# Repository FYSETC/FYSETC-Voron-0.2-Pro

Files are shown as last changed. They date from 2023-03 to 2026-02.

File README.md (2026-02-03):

# FYSETC-Voron-0.2-Pro

This is a project from the VORON community, VORON 0.2. We made a little upgrade and improvement on the basis of this project, and provided a complete set of information. Thanks to the open source materials and support provided by the VORON community, and hope you like it. You can find Voron official information below.

1.VORON 0.2 Official website：https://vorondesign.com/voron0.2

2.VORON 0.2 Official Github：https://github.com/VoronDesign/Voron-0

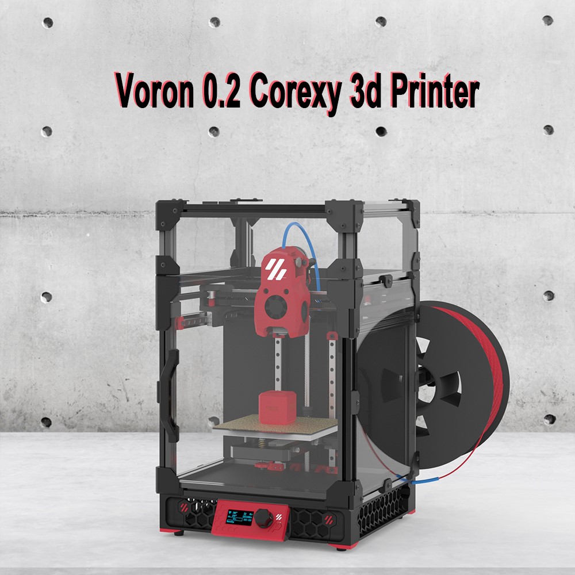
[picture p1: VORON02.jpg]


## 1. Kit advantages:

1.VORON 0 1.3-inch OLED display

2.One-piece CNC hotbed holder 

3.Tophat cover (you can lift the top cover at any time for more convenient maintenance)

4.Sensorless Homing 

5.Upgrade MINI Stealthburner head

6.CNC Lightweight Gantry

7.Print surface: high-quality powder PEI steel plate, good adhesion, flexibility, easy to take molds; platform: MIC6 aluminum finishing, flatness up to 0.05, attached to high-temperature soft magnetic, and additionally designed positioning pillars, which can be fast Place the steel plate in place and not easily move.

8.Sailfish High Flow Hotend（24V 60W）

9.Provide a complete set of crimped terminal Teflon wires, suitable in length, plug and play, and easy to use.

10.It adopts high-precision Stainless steel 440c linear guide MGN7H Z1, precise position and stable operation.

11.Imported silicone thermal mattress, high temperature resistance, built-in over-temperature fuse, high power 24V 75W, fast heating.

12.High-quality motors.

13.Sherpa nano-coating one-piece helical gear kit 

14.Use Klipper firmware
Running on CATALYST V2.0 Motherboard +CM68 Linux core board (based on RK3568, 2GB+32GB) +M36 HUB V1.1 , it can achieve higher printing speed, provide Web control (via WiFi or Ethernet), can connect to a camera.

15.VORON 0 LED light 

## 2. Details

[Voron 0.2 Pro](https://github.com/FYSETC/FYSETC-Voron-0.2/blob/main/0.2/README.md)

[Voron 0.2 R1 Pro](https://github.com/FYSETC/FYSETC-Voron-0.2/blob/main/0.2%20R1/README.md)

[Voron 0.2 R1 Pro V1.1](https://github.com/FYSETC/FYSETC-Voron-0.2-Pro/blob/Pro_R1_1.1/0.2%20R1%20V1.1/README.md)

[Voron 0.2 R1 Pro V1.2](https://github.com/FYSETC/FYSETC-Voron-0.2-Pro/blob/Pro_R1_1.1/0.2%20R1%20V1.2/README.md)

## 3. Community

[Voron community](https://discord.gg/voron)

[FYSETC Facebook group](https://www.facebook.com/groups/238970713918171)

## 4. Buy link

[Aliexpress](https://www.aliexpress.com/item/3256805648574097.html)

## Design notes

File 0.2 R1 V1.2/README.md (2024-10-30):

# Introduction

This is a project from the VORON community, VORON 0.2. We made a little upgrade and improvement on the basis of this project, and provided a complete set of information. Thanks to the open source materials and support provided by the VORON community, and hope you like it. You can find Voron official information below.

1. VORON 0.2 R1 Official website：

https://vorondesign.com/voron0.2

2. VORON 0.2 R1 Official Github:

https://github.com/VoronDesign/Voron-0

# Feature

The new **Voron 0. 2 R1 Pro V1.2 Kit** has a new design for the electronic part, which is easier to connect and configure, and is as close as possible to out-of-the-box use.

# BOM

[Voron 0.2 R1 Pro V1.2](https://github.com/FYSETC/FYSETC-Voron-0.2-Pro/blob/Pro_R1_1.1/0.2%20R1%20V1.2/BOM.md)

# STL changes

Check it.STL has not been modified and can continue to be used [here](https://github.com/FYSETC/FYSETC-Voron-0.2-Pro/tree/Pro_R1_1.1/0.2%20R1%20V1.1/STL).

### Hotend Mount

Check it. [here](https://github.com/FYSETC/FYSETC-Voron-0.2-Pro/tree/main/0.2%20R1%20V1.1/STL/Toolheads/Hotend_Mounts/Fan_Saver)

# Wiring

### R1 Pro V1.1 kit

Following is our Catalyst board wiring diagram for VORON 0.2 R1 Pro V1.1 kit.

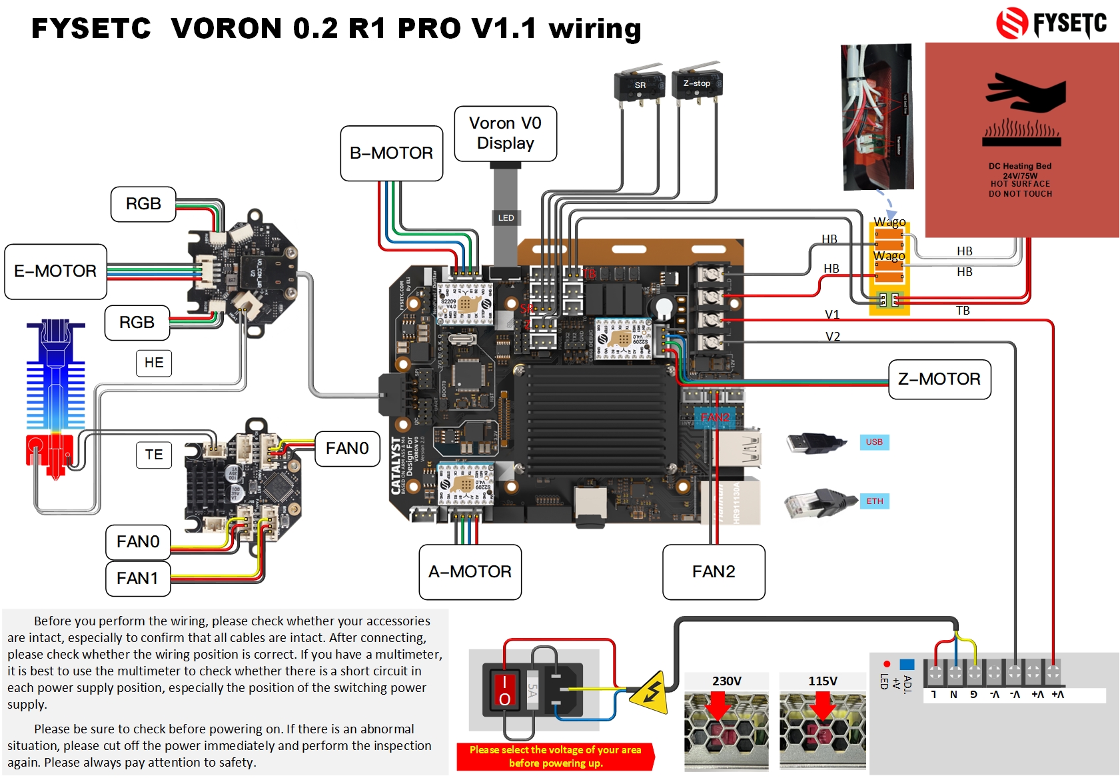
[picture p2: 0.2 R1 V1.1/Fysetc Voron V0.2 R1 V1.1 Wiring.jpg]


# Installation Guide 

Check VORON Assembly manual [here](https://github.com/VoronDesign/Voron-0/tree/Voron0.2/Manuals).

### Page 18 "FRAME - NUT ADAPTER STRIPS"

Kit already comes with PCB style strips to fix the rails

### Page 36 "FRAME - COMPONENT PREP"

Check video [here](https://youtu.be/7Pc5haeAJ8E?si=1WgsYohBYdl78QiE&t=1348)

### Page 120 "X AXIS"

Check video [here](https://youtu.be/7Muv3Jlx758?si=al9ezyuIO8-YeGr-&t=477)

### Page 190 "ELECTRONICS & WIRING"

Following the Catalyst board wiring diagram for VORON 0.2 R1 Pro V1.1 kit.

Check it [here](https://github.com/FYSETC/FYSETC-Voron-0.2-Pro/blob/main/0.2%20R1%20V1.1/Fysetc%20Voron%20V0.2%20R1%20V1.1%20Wiring.pdf).

# Firmware&OS

## CM68 OS 
> [!CAUTION]
> ```diff
> + The control board of this kit has been installed with Klipper OS and MCU Klipper firmware at the factory.
> + And it's pre-configured.
> + As long as the wiring is correct, it can be used after power on.
> - Do not perform the following steps unless you are sure you want to reinstall the firmware.
> ```

The control board uses the CM68 core based on RK3568 as the upper computer of Klipper. Its system is compiled based on Debian 10, and the environment and plug-ins required by Klipper are pre-installed. After burning, it can be used directly.

In general, the pre-installed system can be used directly without re-flashing, unless you encounter unsolvable program problems.

The OS of CM68:

The factory OS is here：
https://github.com/FYSETC/Catalyst_Kit_V2.0/blob/main/software/update_voron0.2_20240108.rar

https://drive.google.com/file/d/1JBLMIpcVtEe9ST9WWUlaOP-ofm4k7y5c/view?usp=drive_link

Update steps:

1. Power on VORON with AC Power. Then plug in the USB3.0 A-A cable into the interface on the upper layer of the blue USB3.0 socket.
2. Open the "RKDevTool_Release",
4. Click the Upgrade Firmware (升级固件) tab, click the Firmware (固件) button to select the firmware, and click the Upgrade button to upgrade  
     
   After selected firmware, it will show like as below  
     
5. Hold the recovery button, click the reset button while holding recovery button (No need to hold reset button), when the RKDevTool found device, release the recovery button.
     
6. Wait for the upgrade to complete. Remember not to cut off the power or unplug the data cable during the process, otherwise the upgrade will fail or even damage the CM68.  
     

## MCU Firmware

<p style="color: red">
<strong>
Do not perform the following steps unless you are sure you want to reinstall the firmware.
</strong>
</p>

If you know the structure of Klipper, then you should understand that the firmware of the MCU is compiled and installed by the host computer (CM68). This is the way we recommend.

Of course, you can also use other methods to burn the MCU, such as through the "STM32CubeProgrammer" on the computer, or with the help of burning tools such as STlink. These need to be studied by yourself, and our control board also provides corresponding interfaces.

The MCU model we use is STM32F446RCT6, with an external 8Mhz crystal oscillator, and uses PA11/PA12 as USB communication. The following is the MCU configuration and burning process:

1. MCU enters DFU mode:

   - Powered off the whole machine
   - Use a jumper cap to connect 3V3 and B0(boot0)
     [img]()
   - Power on the whole machine and wait for it to start

2. Use putty or similar SSH tools to connect to CM68 using IP or host name

    ```
    host name: voron-02-pro.local
    Username: linaro
    Password: linaro
    If you are not very familiar with linux, do not use the root user to log in. Misoperation may cause damage to the system.
    Username: root
    Password: root
    ```

3. Configure the firmware:

    - use "lsusb" to ensure the mcu enter dfu mode,

       ```
       lsusb
       ```

    - configure the firmware
    
       ```
       cd ~/klipper
       make clean
       make menuconfig
       ```
       
4. update the firmware and reboot

    - Compile and burn the firmware:
    
      ```
       make flash FLASH_DEVICE=0483:df11
      ```
    
    - Powered off the whole machine
    - Use a jumper cap to connect B0(boot0) and G(GND)
    - Power on the whole machine and wait for it to start
  
5.If you need update the M36 tool Board,Please refer to https://github.com/FYSETC/M36_HUB_V1

# Print

## Connect via Ethernet

The control board defaults to obtain IP automatically, make sure your router can provide DHCP service normally. You only need to plug in the Internet cable, and when you see the green and yellow lights on, indicates that it is connected to the network.

You have two methods to login the mainsail webpage:

### IP address
you need to go to your router to find the device named voron-02-pro, and write down the IP address
### Host name
The kit has already installed the required plug-ins, and you can access the mainsail page through the pre-set host name: voron-02-pro.local

## Connect via WiFi

- First connect the machine to your LAN via Ethernet, make sure you can log in to CM68 via SSH.
- Plug the included USB wifi into any USB interface on CATALYST board
- Use the following command checks whether the wifi module is recognized:
```
sudo ifconfig
```
- Use the following command to connect to wifi
```
sudo wifi_sta_start.sh ssid password
```
- Use the following command checks whether the wifi module is connected to your router, and get the ip address:
```
sudo ifconfig
```

# FAQ

## 1. Can't find mcu/unable to connect to mcu
Reason:
       It may be that the status of boot0 is uncertain, causing the STM32 to enter the DFU mode, resulting in the connection error.
Solution:
   - Powered off the whole machine
   - Use a jumper cap to connect B0(boot0) and G(GND)
   - Power on the whole machine and wait for it to start
## 2. Mcu firmware version too low
Reason:
The factory version of the Klipper host is the same as that of the MCU. Maybe you have clicked the update button on the mainsail webpage to update the Klipper host. As a result, the version of the host is newer than the firmware of the MCU.
Solution:
update the mcu firmware: Refer to the Firmware&OS==>MCU Firmware
## 3. Temperature error
Reason:
You may have forgotten to connect the MX3.0 16P cable, or it may not be connected firmly.
Solution:
Make sure the MX3.0 16P cable is connected and secure.
## 4. How to use the accelerometer
Refer to Klipper document: 
https://www.klipper3d.org/Resonance_Compensation.html

## 5. Wifi Connection Issues
If you are having problems with your Catalyst wifi, please fix using the following solution. 

SSH into the Catalyst, and run the following command `sudo nano /etc/network/interfaces`

Once you have run the command, add the following lines 

```
auto wlan0
iface wlan0 inet dhcp
wpa-ssid Your Network Name Here
wpa-psk Your Password Goes Here
```
example if your wifi name is fysetcwifi and password was ItRocks:
```
auto wlan0
iface wlan0 inet dhcp
wpa-ssid fysetcwifi
wpa-psk ItRocks
```

# Support
Voron community: 
https://discord.gg/voron
FYSETC Facebook group: 
https://www.facebook.com/groups/238970713918171
FYSETC Discord:
https://discord.gg/T3XcJPgr 
# Buy Link
https://www.aliexpress.com/item/3256805648574097.html

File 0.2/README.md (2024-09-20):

# FYSETC-Voron-0.2-Pro

This is a project from the VORON community, VORON 0.2. We made a little upgrade and improvement on the basis of this project, and provided a complete set of information. Thanks to the open source materials and support provided by the VORON community, and hope you like it. You can find Voron official information below.

1.VORON 0.2 Official website：https://vorondesign.com/voron0.2

2.VORON 0.2 Official Github：https://github.com/VoronDesign/Voron-0



## 1. Kit advantages:

1.VORON 0 1.3-inch OLED display

2.One-piece CNC hotbed holder 

3.Tophat cover (you can lift the top cover at any time for more convenient maintenance)

4.Sensorless Homing 

5.Upgrade MINI Stealthburner head

6.CNC Lightweight Gantry

7.Print surface: high-quality powder PEI steel plate, good adhesion, flexibility, easy to take molds; platform: MIC6 aluminum finishing, flatness up to 0.05, attached to high-temperature soft magnetic, and additionally designed positioning pillars, which can be fast Place the steel plate in place and not easily move.

8.Tornado hotend, check the features [here](https://github.com/FYSETC/FYSETC-Voron-0/blob/main/Tornado_hotend.md). (Please installation guide on our [youtube](https://www.youtube.com/watch?v=a5HArBp4h3s))

9.Provide a complete set of crimped terminal Teflon wires, suitable in length, plug and play, and easy to use.

10.It adopts high-precision Stainless steel 440c linear guide, precise position and stable operation

11.Imported silicone thermal mattress, high temperature resistance, built-in over-temperature fuse, high power 24V 75W, fast heating.

12.High-quality motors.

13.Contains VORON V0 UMBILICAL FRAME and VORON V0 UMBILICAL TOOL HEAD

14.Use Klipper firmware
Running on Cheetah v3.0 and Raspberry Pi 4 2GB, it can achieve higher printing speed, provide Web control (via WiFi or Ethernet), can connect to a camera.

## 2. BOM

[Voron 0.2 Pro](https://github.com/FYSETC/FYSETC-Voron-0.2/blob/main/0.2/BOM.md)

## 3. Modified STLs (2023.03.03)

So we modify these STLs base on the originals. You can find them in our `github` or `gitee`.

`FramePCBCover X1.stl` : For VORON V0 UMBILICAL FRAME[github](https://github.com/FYSETC/FYSETC-Voron-0.2/blob/main/STL/ADD/FramePCBCover%20X1.STL)

`ToolheadSpacer_with_StrainRelief X1`:For VORON V0 UMBILICAL TOOL HEAD [github](https://github.com/FYSETC/FYSETC-Voron-0.2/blob/main/STL/ADD/ToolheadSpacer_with_StrainRelief%20X1.STL)

`VORON0.1 X2.stl` :For CNC Lightweight Gantry [github](https://github.com/FYSETC/FYSETC-Voron-0.2/blob/main/STL/ADD/VORON0.1%20X2.stl)

`LJY-B01 X1.stl`:For One-piece CNC hotbed holder [github](https://github.com/FYSETC/FYSETC-Voron-0.2/blob/main/STL/ADD/LJY-B01%20X1.STL)

`Drag Chain Spacer X1.stl`:For One-piece CNC hotbed holder Chain [github](https://github.com/FYSETC/FYSETC-Voron-0.2/blob/main/STL/ADD/Drag%20Chain%20Spacer%20X1.STL)

## 4. Installation Guide

### 4.1 VORON Assembly manual

Check it [here](https://github.com/VoronDesign/Voron-0/tree/Voron0.2/Manuals).

### 4.2 Tornado Hotend installation

Please check it on our [youtube](https://www.youtube.com/watch?v=a5HArBp4h3s).

## 5. Wiring

Following is our Cheetah v3.0 board wiring diagram for VORON 0.2 pro kit.



## 6. Firmware&OS

After you finish assembling and inspecting, be sure to wire according to the wiring diagram, and make sure that all positive and negative poles are not reversed before powering on. If you have a multimeter, it is best to check again that the power input port is not short-circuited.
Next we start configuring the firmware:
### 6.1. Install the Raspberry Pi

There is a Micro SD Card with the mainsail OS system burned in our kit. The capacity is 16GB. You need to insert it into the card slot of the Raspberry Pi, and connect the Raspberry Pi to the main board with a USB cable and a power cable (it is a 6-core Dupont cable, which contains a serial port, but the power supply is made by default, and the serial port is a spare).

If you need to reinstall the system, you can refer to the following link:
https://docs-os.mainsail.xyz/getting-started/raspberry-pi-os-based

### 6.2. Configure the Cheetah Board

Use SSH software to connect to your Raspberry Pi and enter the following command:
```
lsusb
```
You should see the device as shown below:

If not, please go back and check the power supply and wiring of the motherboard to ensure that each power indicator light is on.
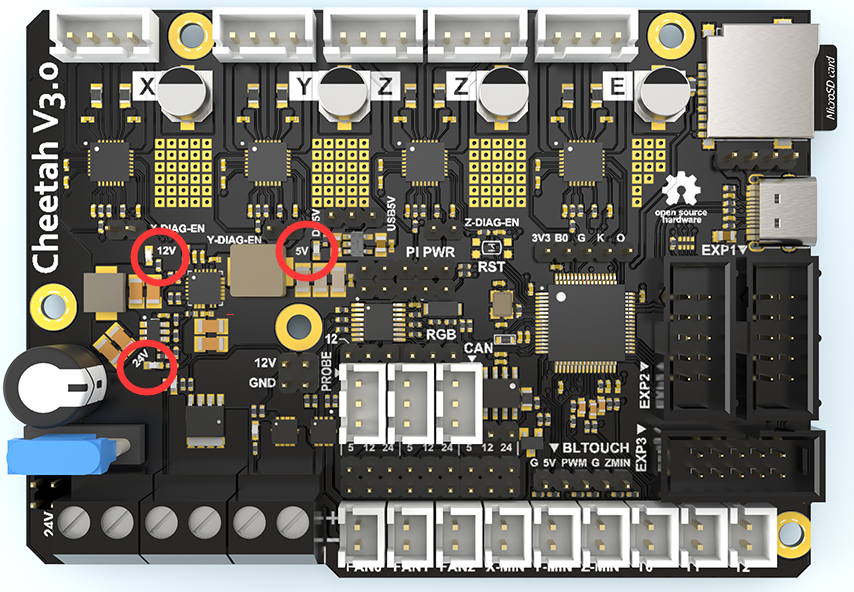
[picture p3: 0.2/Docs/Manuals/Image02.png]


Enter the following command to get the board ID:
```
ls /dev/serial/by-id
```
Copy the ID with Crtl+C


Use the browser to enter the IP address of the Raspberry Pi to enter the mainsail interface
Click on MACHINE
Click printer.cfg in the list to enter the editing interface
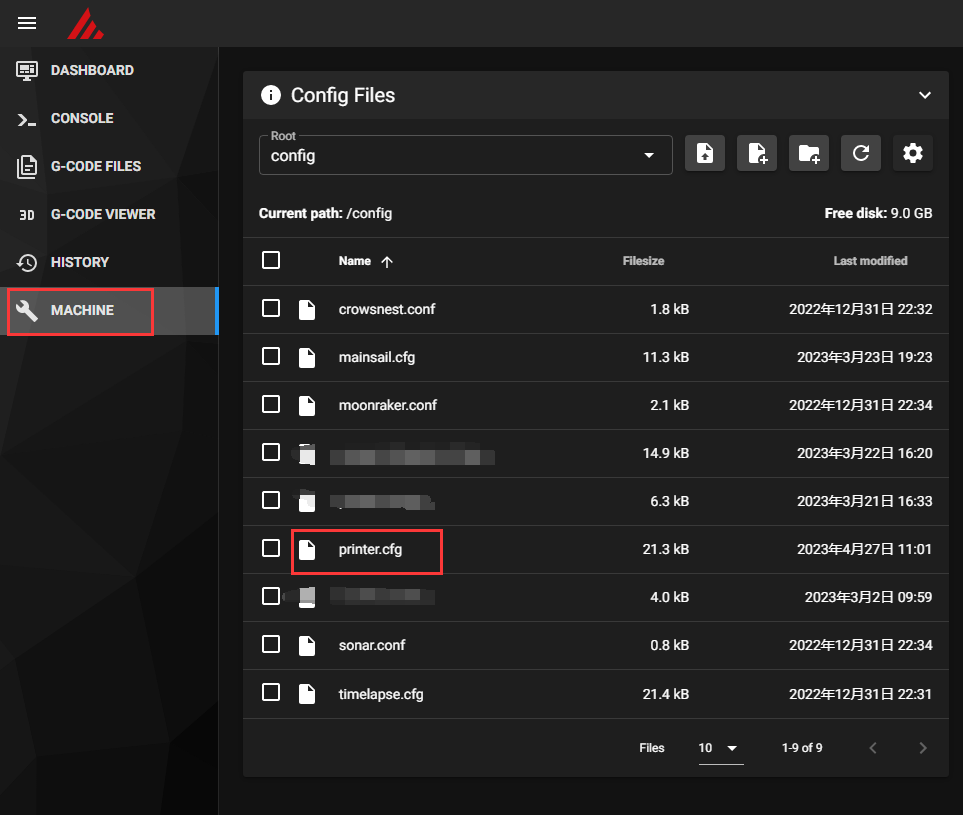
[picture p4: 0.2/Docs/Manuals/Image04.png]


Replace the ID in the [mcu] section
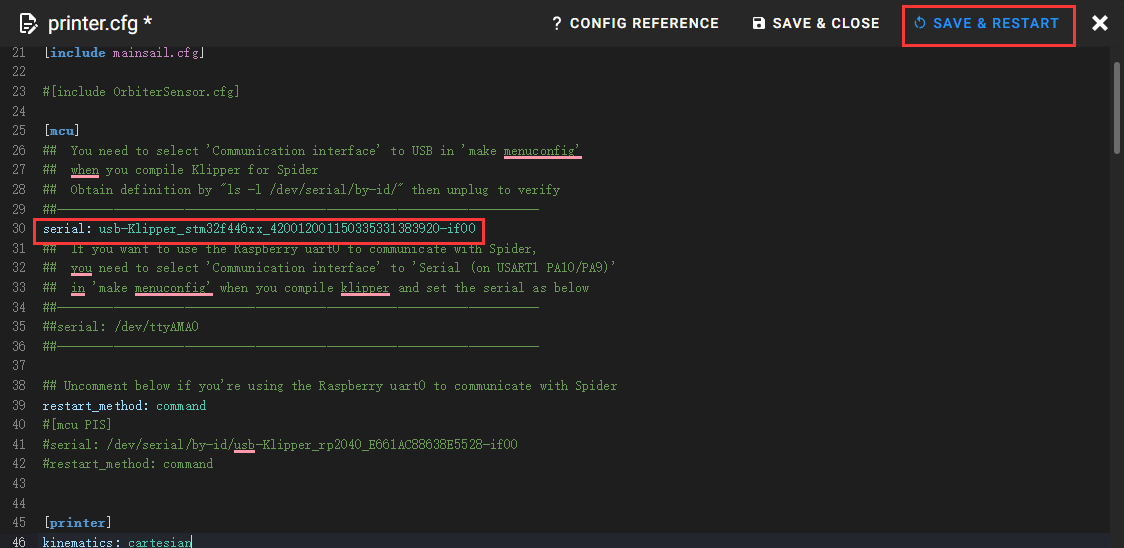
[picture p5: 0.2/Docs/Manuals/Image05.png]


Click SAVE & RESTART

If it goes well, the system will automatically jump to Dashboard, and you can see the temperature curve

## 6.3.1 Build Firmware Image

* Login to the Raspberry Pi via ssh
* Run the following:

   ```
   cd ~/klipper
   make clean
   make menuconfig
   ```

* In the menu structure there are a number of items to be selected.
  * Select "Enable extra low-level configuration options"
  * Set the micro-controller architecture is set to `STMicroelectronics STM32`
  * Set the Processor model to `STM32F446`
  * **Many people have been unable to connect to the MCU because of the bootloader problem, so we recommends choosing a mode without a bootloader.**
  * Set the Clock Reference to `12 MHz crystal`
  * Set the Communication interface to `USB (on PA11/PA12)`  

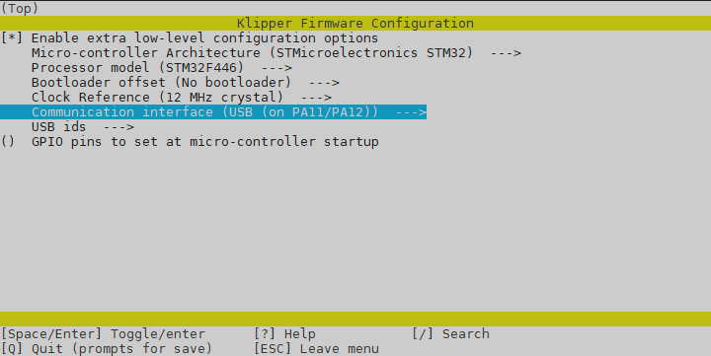
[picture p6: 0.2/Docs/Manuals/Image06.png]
   

* Once the configuration is selected, press `q` to exit, and "Yes" when  asked to save the configuration.

* Run the command `make`
* The `make` command, when completed, creates a firmware file **klipper.bin** which is stored in the folder `/home/pi/klipper/out`.  

## 6.3.2 Firmware Installation

* Requires a USB connection
* Requires the installation of an extra jumper on the Cheetah V3 ( short the 3V3 and BT0)
* Does NOT require a microSD card

1. Power off the Cheetah V3
2. Install a jumper between BT0 and 3V3

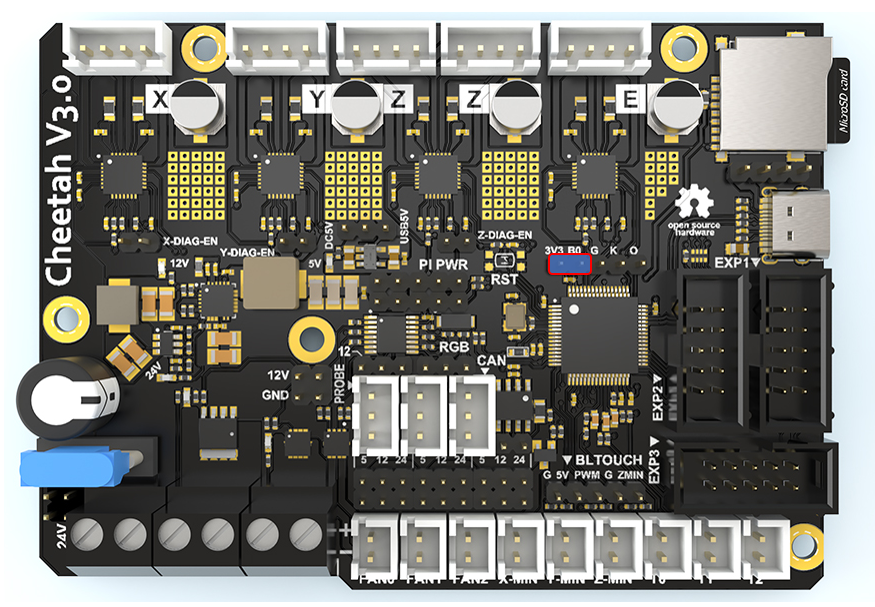
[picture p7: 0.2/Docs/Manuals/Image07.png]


3. Connect Cheetah V3 & Pi via USB
4. Power on Cheetah V3
5. From your ssh session, run
    ```
    cd ~/klipper
    ```
    to make sure you are in the correct directory
6. Run 
    ```
     lsusb
    ```
    and find the ID of the DFU device.
    
    
    
7. Run 
    ```
     make flash FLASH_DEVICE=0483:df11
    ```
    In general, the DFU mode of STM32 is this ID, if not, replacing 0483:df11 with the ID from the previous step
 8. If everything goes well, you will see the words SUCCESSFUL.
  
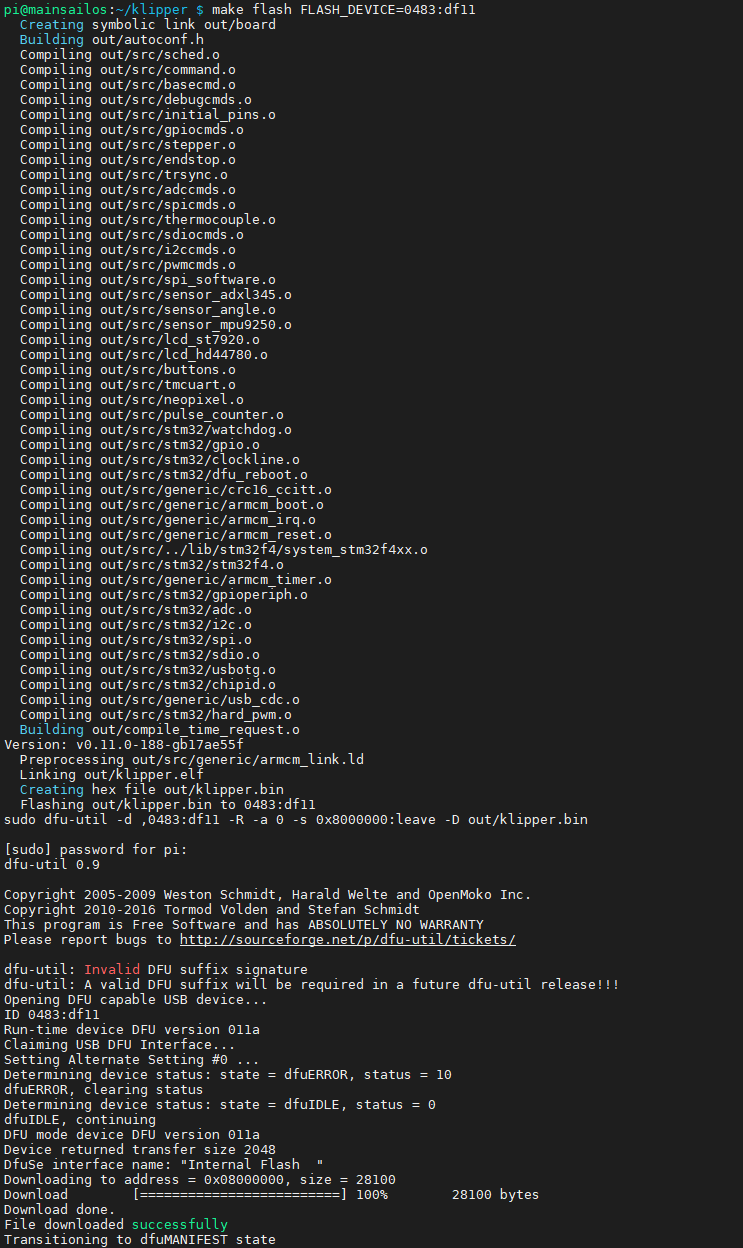
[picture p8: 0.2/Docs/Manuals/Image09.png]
    
    
 9. Power off the Cheetah V3

 10. Move the jumper to BT0 & GND (When the STM32 is turned on, BT0 should be at a low level, and it is also possible to hang it in the air, but in order to avoid unpredictable problems, it is better to short-circuit BT0 and GND here, which is more secure.)

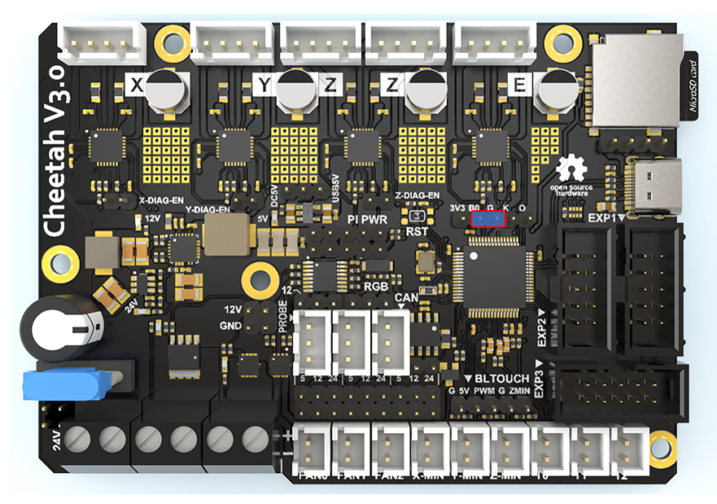
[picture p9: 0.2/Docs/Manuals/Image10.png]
   

 11. Power up the Cheetah V3

 12. You can confirm that the flash was successful by running `ls /dev/serial/by-id`.  If the flash was successful, this should now show a klipper device, similar to:

     

   (note: this test is not applicable if the firmware was compiled for UART, rather than USB)

**Important:** If the Cheetah V3 is not powered with 12-24V, Klipper will be unable to communicate with the TMC drivers via UART and the Cheetah V3 will automatically shut down.

## 7. Community

[Voron community](https://discord.gg/voron)

[FYSETC Facebook group](https://www.facebook.com/groups/238970713918171)

## 8. Buy link

[Aliexpress](https://www.aliexpress.us/item/3256805148633512.html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)

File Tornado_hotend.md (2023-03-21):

# Tornado hotend

## Features :

1. 全金属

   | Parts        | Material |
   | ------------ | -------- |
   | 加热块和喷头 | 铜镀镍   |
   | 喉管         | 钛合金   |
   | 散热器和接头 | 航空铝   |

2. 可作为近程和远程挤出机热端使用

3. 兼容龙挤出机孔位

4. 配有全金属和 PTFE 两种喉管，全金属喉管可以打印高温材料，PTFE 喉管用于打印常规耗材，表面更光滑

1. All metal 

   | Parts                                     | Material            |
   | ----------------------------------------- | ------------------- |
   | heat block and nozzle                     | nickel plated brass |
   | heatbreak                                 | titanium alloy      |
   | heat sink and pneumatic connector coupler | aviation aluminum   |

2. Can be used for bowden extruder and direct drive extruder.

3. Compatible with the hole positions of dragon hotend

4. Provide both metal heatbreak and PTFE heatbreak : metal heatbreak for high temp filament, PTFE for regular filament have smoother surface.

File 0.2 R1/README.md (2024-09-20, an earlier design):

# Introduction

This is a project from the VORON community, VORON 0.2. We made a little upgrade and improvement on the basis of this project, and provided a complete set of information. Thanks to the open source materials and support provided by the VORON community, and hope you like it. You can find Voron official information below.

1. VORON 0.2 Official website：

https://vorondesign.com/voron0.2

2. VORON 0.2 Official Github:

https://github.com/VoronDesign/Voron-0

# Feature

The new **Voron 0. 2 Pro R1 Kit** has a new design for the electronic part, which is easier to connect and configure, and is as close as possible to out-of-the-box use.

# BOM

[Voron 0.2 R1 Pro](https://github.com/FYSETC/FYSETC-Voron-0.2/blob/main/0.2%20R1/BOM.md)

# STL changes

### Additional STLs

Check it [here](https://github.com/FYSETC/FYSETC-Voron-0.2-Pro/tree/main/0.2%20R1/STL/ADD).

### Hotend Mount

Check it [here](https://github.com/FYSETC/FYSETC-Voron-0.2-Pro/blob/main/0.2%20R1/STL/Toolheads/Hotend_Mounts/Fan_Saver/%5Ba%5D_FS_Hotend_Mount_Dragon.stl)

### Unnecessary STLs
- Rear_Bed_Mount_Right_x1.stl
- Front_Bed_Mount_x1.stl
- Rear_Bed_Mount_Left_x1.stl
- Drag_Chain_Spacer_x1.stl
- PCB_DIN_Clip_x2.stl
- PCB_DIN_Clip_x2.stl
- Fan_Mount_Bottom_x1.stl
- VHB_DIN_Mount.STL
- VHB_DIN_Mount.STL
- Fan_Mount_Top_x1.stl
- M2_Nut_Adapter_Rotated_x5.stl

# Wiring

### R1 Pro kit

Following is our Catalyst board wiring diagram for VORON 0.2 R1 pro kit.

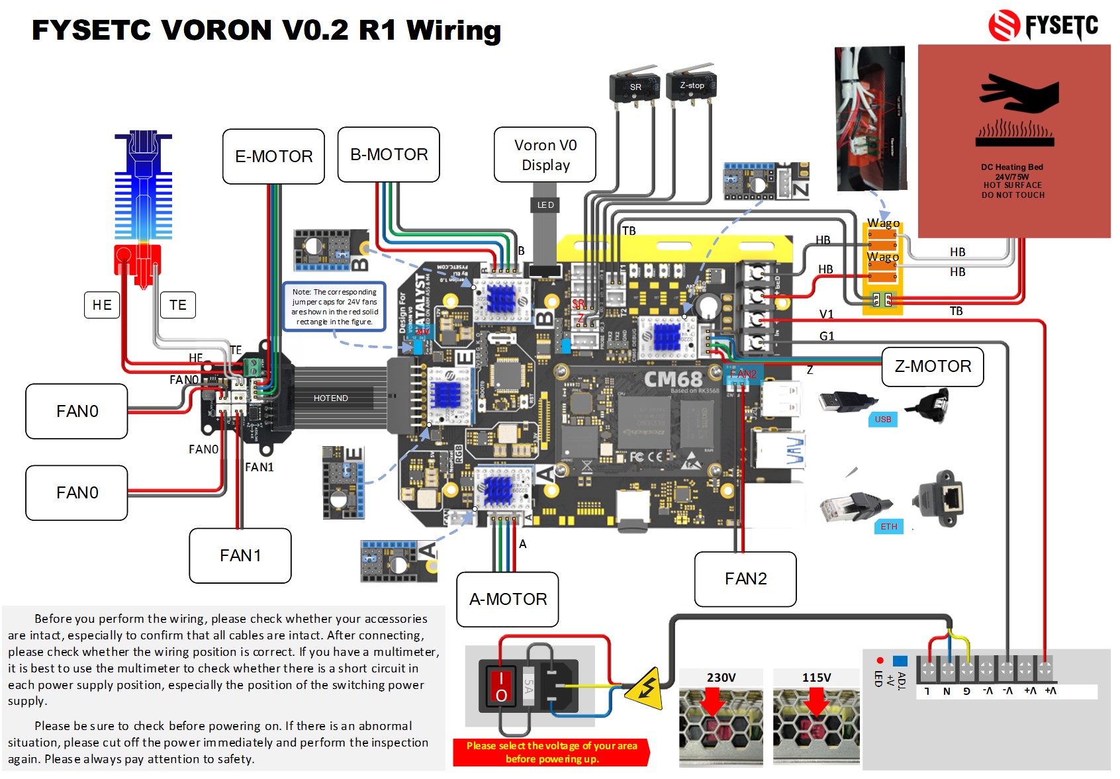
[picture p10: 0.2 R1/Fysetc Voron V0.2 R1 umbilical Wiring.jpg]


# Installation Guide 

Check VORON Assembly manual [here](https://github.com/VoronDesign/Voron-0/tree/Voron0.2/Manuals).

### Page 18 "FRAME - NUT ADAPTER STRIPS"

Kit already comes with PCB style strips to fix the rails

### Page 36 "FRAME - COMPONENT PREP"

Check video [here](https://youtu.be/7Pc5haeAJ8E?si=1WgsYohBYdl78QiE&t=1348)

### Page 120 "X AXIS"

Check video [here](https://youtu.be/7Muv3Jlx758?si=al9ezyuIO8-YeGr-&t=477)

### Page 190 "ELECTRONICS & WIRING"

Following the Catalyst board wiring diagram for VORON 0.2 pro R1 kit.

Check it [here](https://github.com/FYSETC/FYSETC-Voron-0.2-Pro/blob/main/0.2%20R1/Fysetc%20Voron%20V0.2%20R1%20umbilical%20Wiring.pdf).

# Firmware&OS

## CM68 OS 

<p style="color: green">
<strong>
The control board of this kit has been installed with Klipper OS and MCU Klipper firmware at the factory. And it's pre-configured.
As long as the wiring is correct, it can be used after power on.
</strong>
</p>

<p style="color: red">
<strong>
Do not perform the following steps unless you are sure you want to reinstall the firmware.
</strong>
</p>

The control board uses the CM68 core based on RK3568 as the upper computer of Klipper. Its system is compiled based on Debian 10, and the environment and plug-ins required by Klipper are pre-installed. After burning, it can be used directly.

In general, the pre-installed system can be used directly without re-flashing, unless you encounter unsolvable program problems.

The OS of CM68:

https://drive.google.com/file/d/1JBLMIpcVtEe9ST9WWUlaOP-ofm4k7y5c/view?usp=drive_link

Update steps:

1. plugin the USB3.0 A-A cable into the interface on the upper layer of the blue USB3.0 socket,
2. open the "RKDevTool_Release",
3. hold the recovery button, click the reset button, when the RKDevTool found device, release the 2 buttons
4. Click the Upgrade Firmware tab, click the Firmware button to select the firmware, and click the Upgrade button to upgrade
5. Wait for the upgrade to complete. Remember not to cut off the power or unplug the data cable during the process, otherwise the upgrade will fail or even damage the CM68.

## MCU Firmware

<p style="color: red">
<strong>
Do not perform the following steps unless you are sure you want to reinstall the firmware.
</strong>
</p>

If you know the structure of Klipper, then you should understand that the firmware of the MCU is compiled and installed by the host computer (CM68). This is the way we recommend.

Of course, you can also use other methods to burn the MCU, such as through the "STM32CubeProgrammer" on the computer, or with the help of burning tools such as STlink. These need to be studied by yourself, and our control board also provides corresponding interfaces.

The MCU model we use is STM32F401RCT6, with an external 8Mhz crystal oscillator, and uses PA11/PA12 as USB communication. The following is the MCU configuration and burning process:

1. MCU enters DFU mode:

   - Powered off the whole machine
   - Use a jumper cap to connect 3V3 and B0(boot0)
     [img]()
   - Power on the whole machine and wait for it to start

2. Use putty or similar SSH tools to connect to CM68 using IP or host name

    ```
    host name: voron-02-pro.local
    Username: linaro
    Password: linaro
    If you are not very familiar with linux, do not use the root user to log in. Misoperation may cause damage to the system.
    Username: root
    Password: root
    ```

3. Configure the firmware:

    - use "lsusb" to ensure the mcu enter dfu mode,

       ```
       lsusb
       ```

    - configure the firmware
    
       ```
       cd ~/klipper
       make clean
       make menuconfig
       ```

4. update the firmware and reboot

    - Compile and burn the firmware:
    
      ```
       make flash FLASH_DEVICE=0483:df11
      ```
    
    - Powered off the whole machine
    - Use a jumper cap to connect B0(boot0) and G(GND)
    - Power on the whole machine and wait for it to start

# Print

## Connect via Ethernet

The control board defaults to obtain IP automatically, make sure your router can provide DHCP service normally. You only need to plug in the Internet cable, and when you see the green and yellow lights on, indicates that it is connected to the network.

You have two methods to login the mainsail webpage:

### IP address
you need to go to your router to find the device named voron-02-pro, and write down the IP address
### Host name
The kit has already installed the required plug-ins, and you can access the mainsail page through the pre-set host name: voron-02-pro.local

## Connect via WiFi

- First connect the machine to your LAN via Ethernet, make sure you can log in to CM68 via SSH.
- Plug the included USB wifi into any USB interface on CATALYST board
- Use the following command checks whether the wifi module is recognized:
```
sudo ifconfig
```
- Use the following command to connect to wifi
```
sudo wifi_sta_start.sh ssid password
```
- Use the following command checks whether the wifi module is connected to your router, and get the ip address:
```
sudo ifconfig
```

# FAQ

## 1. Can't find mcu/unable to connect to mcu
Reason:
       It may be that the status of boot0 is uncertain, causing the STM32 to enter the DFU mode, resulting in the connection error.
Solution:
   - Powered off the whole machine
   - Use a jumper cap to connect B0(boot0) and G(GND)
   - Power on the whole machine and wait for it to start
## 2. Mcu firmware version too low
Reason:
The factory version of the Klipper host is the same as that of the MCU. Maybe you have clicked the update button on the mainsail webpage to update the Klipper host. As a result, the version of the host is newer than the firmware of the MCU.
Solution:
update the mcu firmware: Refer to the Firmware&OS==>MCU Firmware
## 3. Temperature error
Reason:
You may have forgotten to connect the MX3.0 16P cable, or it may not be connected firmly.
Solution:
Make sure the MX3.0 16P cable is connected and secure.
## 4. How to use the accelerometer
Refer to Klipper document: 
https://www.klipper3d.org/Resonance_Compensation.html

## 5. Wifi Connection Issues
If you are having problems with your Catalyst wifi, please fix using the following solution. 

SSH into the Catalyst, and run the following command `sudo nano /etc/network/interfaces`

Once you have run the command, add the following lines 

```
auto wlan0
iface wlan0 inet dhcp
wpa-ssid Your Network Name Here
wpa-psk Your Password Goes Here
```
example if your wifi name is fysetcwifi and password was ItRocks:
```
auto wlan0
iface wlan0 inet dhcp
wpa-ssid fysetcwifi
wpa-psk ItRocks
```

# Support
Voron community: 
https://discord.gg/voron
FYSETC Facebook group: 
https://www.facebook.com/groups/238970713918171
FYSETC Discord:
https://discord.gg/T3XcJPgr 
# Buy Link
https://www.aliexpress.us/item/3256805148633512.html

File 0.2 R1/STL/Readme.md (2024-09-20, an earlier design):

Update 25/11/2023: Unecessary bed parts removed.

# [Printed Parts Guide](https://docs.google.com/spreadsheets/d/1MSgTiXazJwyfcTe7QqNIMWwQ_lfM8cOXmiMWPZ2HkEI/copy)

This document lists all of the printed parts with images, names, and where they are used in the assembly manual as well as other helpful notes

# Part File Naming Guide

**QUANTITY REQUIRED**

*[a]_Thumb_Nut_x3.stl*  
Any file that ends with “_x#” is telling you the quantity of that part required to build the machine.

**BUILD SPECIFIC PARTS**

*Headless_Skirt_Insert.stl*  
Any file name that does **NOT** end with a quantity designation is a part that needs to be choosen based on the specific components and options you want for your build, things like controller boards, ADXL mounts or the Bowden toolhead are exampls of parts that will not have quantities and can be printed or not based on your choosing. 

**ACCENT COLOR**

*[a]_Tensioner_Knob_x2.stl*  
We have added “[a]” to the front of any STL file that is intended to be printed with accent color. The parts are marked with a heart in the manual when they first appear. 

**PRIMARY COLOR**

*B_Drive_Frame_Lower_x1.stl*  
These files will have nothing at the start of the filename.

**CLEAR / TRANSLUCENT**

*[c]_Display_Diffuser_x1.stl*  
Any file that begins with "[c]" is intended to be printed in a clear or translucent color that allows light to penetrate through it.

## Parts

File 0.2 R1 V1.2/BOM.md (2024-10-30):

# Bill of Materials

| Index | Sort | Component | Qty | Note |
| ----- | --- | --- | --- | --- |
| 1 | Fasteners | Voron V0.2 R1 fasteners Pack （Black）12.9 | 1 SET  | |
| 2 | Extruder Hardware | Sherpa nano-coating one-piece helical gear kit (Includes all accessories) | 1 SET  | Upgrade |
| 3 | Frame | Voron 0.2 R1 1515 aluminum extrusion profile frame kit（Tophat height 100mm） | 27 PCS | Upgrade |
| 4 | Electronics | Meanwell LRS-150-24 | 1 PC | |
| 5 | Electronics | FYSETC CATALYST V2.1 | 1 PC | Upgrade |
| 6 | Electronics | Voron V0 1.3 inch OLED Display Screen | 1 PC | |
| 7 | Electronics | CM68 Linux core board (based on RK3568, 2GB+32GB), Raspberry Pi 4 replacement | 1 PC | Upgrade |
| 8 | Electronics | MicroSD Card 16G | 1 PC | |
| 9 | Electronics | NEMA14 Stepper Motor 40Ncm 35HSH7402-24B-60A(check [here](https://github.com/FYSETC/FYSETC-Voron-0.2-Pro/blob/main/0.2%20R1%20V1.1/Docs/Stepper%20motor%20parameters/35HSH7402-24B-60A.pdf)) | 2 PCS  | |
| 10 | Electronics | NEMA17 Stepper Motor (34mm max) with integrated lead screw 200mm T8x8 42HSC1433B-200N8(check [here](https://github.com/FYSETC/FYSETC-Voron-0.2-Pro/blob/main/0.2%20R1%20V1.1/Docs/Stepper%20motor%20parameters/42HSC1433B-200N8.pdf) Teflon wire | 1 PC | Upgrade |
| 11 | Electronics | NEMA14 36mm round pancake Stepper Motor with 10 tooth spur gear G36HSY4405-6D-50(check [here](https://github.com/FYSETC/FYSETC-Voron-0.2-Pro/blob/main/0.2%20R1%20V1.1/Docs/Stepper%20motor%20parameters/G36HSY4405-6D-50.pdf)) Teflon wire | 1 PC | |
| 12 | Electronics | 3010  Dual Ball blower fans 24V | 2 PCS  | |
| 13 | Electronics | 3010  Dual Ball axial fan 24V | 2 PCS  | |
| 14 | Electronics | Omron Micro Switch（Z-endstop With wire） | 1 PC | |
| 15 | Electronics | C13 Power Cord | 1 PC | |
| 16 | Electronics | AC Inlet （ With Fuse ） | 1 SET  | |
| 17 | Electronics | Sailfish High Flow Hotend （ all-metal hotend） | 1 PC | Upgrade |
| 18 | Electronics | 24V 60W Heater | 1 PC | Upgrade |
| 19 | Electronics | Thermistor NTC 100K B3950 | 1 PC | Upgrade |
| 20 | Electronics | VHB tape (20mm) | 1 PC | |
| 21 | Electronics | Omron Micro Switch（Filament sensor With wire） | 1 PC | Add |
| 22 | Cables | M36 HUB  cable | 1 SET  | upgrade |
| 23 | Cables | M36 HUB V1.1 | 1 SET  | upgrade |
| 24 | Cables | Voron 0.2 cables kit（All cables are connected to the terminals，Plug and play，Label buckle）Teflon wire | 1 SET  | |
| 25 | Cables | 2mmx120mm zip ties | 50 PCS | |
| 26 | Cables | Network cable | 1 PC | |
| 27 | Electronics | VORON 0 LED light | 2 PCS  | add |
| 28 | Motion | F623-RS Bearing | 24 PCS | |
| 29 | Motion | MGN7H Z1 Linear Rail with Carriage (150mm) Stainless steel 440C | 5 PCS  | upgrade |
| 30 | Motion | GT2 20T (6mm wide) (5mm bore) | 2 PCS  | |
| 31 | Motion | 6RF Open Belt 6mm GT2 (2.1 meters) | 1 PC | |
| 32 | Motion | T8 flange Nut 8mm Lead --anti-backlash | 1 PC | |
| 33 | Buildplate | Aluminum Build Plate (MIC6) 120x120mm | 1 PC | Positionable steel plate like prusa |
| 34 | Buildplate | Silicone DC 24V Heater 100x100mm 75W （Faster heating rate）with plug | 1 PC | |
| 35 | Buildplate | Thermal Fuse (125C) with plug | 1 PC | |
| 36 | Buildplate | Yellow die springs 8x4x20mm | 3 PCS  | |
| 37 | Buildplate | PEI Powder Coated Spring Steel Flex Buildplate 120x120mm notched | 1 PC | |
| 38 | Buildplate | Magnetic sheet for spring steel plate 120x120mm | 1 PC | |
| 39 | Panels | Voron 0.2 Acrylic Panels kit | 1 SET  | |
| 40 | Bowden | Bowden Fitting ECAS04 | 3 PCS  | Increase Quantity |
| 41 | Bowden | Bowden Tubing 4mmOD 1.9mmID (1meter) | 1 PC | |
| 42 | Bowden | Bowden Tubing 4mmOD 2.5mmID (1meter) | 1 PC | add |
| 43 | Misc | Tank Chain 7x7mm | 1 PC | |
| 44 | Misc | Little Rubber Feet (14x11x11mm) | 4 PCS  | |
| 45 | Misc | XH2.54 2/3/4 Pin Plastic shell | 1 SET  | |
| 46 | Misc | 6mm x 3mm Round Neodymium Magnets | 8 PCS  | |
| 47 | Misc | Weaving casing φ8mm length 180mm | 1 SET  | |
| 48 | Misc | Weaving casing φ8mm length 205mm | 1 SET  | |
| 49 | Misc | FYSETC label | 1 PC | |
| 50 | Misc | Voron V0 Full Metal Heat Bed Frame | 1 SET  | upgrade |
| 51 | Misc | Voron V0 Full metal gantry Super light CNC Part | 1 PC | upgrade |
| 52 | Misc | VORON V0 Rail retainer with nut | 10 PCS | upgrade |
| 53 | Tools | Cutting pliers | 1 PC | |
| 54 | Tools | Hexagonal wrenchs | 1 SET  | |
| 55 | Misc | Thermal silica | 1 PC | |
| 56 | Misc | USB extension cable | 1 PC | Add |
| 57 | Misc | RJ45 extension cable | 1 PC | Add |
| 58 | Misc | USB WiFi | 1 PC | Add |
| 59 | Misc | MR85ZZ Ball bearing | 1 PC | Add |
| 60 | Misc | FYSETC Voron V0.2 Wiring manual | 1 SET  | |

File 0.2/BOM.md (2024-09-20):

# Bill of Materials

| Index | Sort | Component | Qty | Note |
| ----- | :--- | --- | --- | --- |
| 1 | Fasteners | Voron V0.2 fasteners Pack  （Black）12.9 | 1 SET  | |
| 2 | Extruder Hardware | BMG Extruder gear kit(Includes all accessories) | 1 SET  | |
| 3 | Frame | Voron 0.2 1515 aluminum extrusion profile frame kit | 27 PCS | |
| 4 | Electronics | Meanwell LRS-150-24 | 1 PC | |
| 5 | Electronics | FYSETC  cheetah 3.0 | 1 PC | |
| 6 | Electronics | Voron V0  1.3 inch OLED Display Screen | 1 PC | |
| 7 | Electronics | Raspberry Pi 4B 2GB | 1 PC | Optional |
| 8 | Electronics | MicroSD Card 16G | 1 PC | |
| 9 | Electronics | NEMA14 Stepper Motor 40Ncm 35HSH7402-24B-300A(check [here](https://github.com/FYSETC/FYSETC-MOTORS/tree/main/35HSH7402-24B-300A)) | 2 PCS  | |
| 10 | Electronics | NEMA17 Stepper Motor (34mm max) with integrated lead screw 200mm T8x8 42HSC1404B-200N8(check [here](https://github.com/FYSETC/FYSETC-MOTORS/tree/main/42HSC1404B-200N8)) Teflon wire | 1 PC | |
| 11 | Electronics | NEMA14 36mm round pancake Stepper Motor with 10 tooth spur gear G36HSY4405-6D-80(check [here](https://github.com/FYSETC/FYSETC-MOTORS/tree/main/G36HSY4405-6D-80)) Teflon wire | 1 PC | |
| 12 | Electronics | 3010 blower fans 24V | 2 PCS  | |
| 13 | Electronics | 3010 axial fan 24V | 2 PCS  | |
| 14 | Electronics | Micro Switch（With wire） | 1 PC | |
| 15 | Electronics | C13 Power Cord | 1 PC | |
| 16 | Electronics | AC Inlet （ With Fuse ） | 1 SET  | |
| 17 | Electronics | Tornodo hotend（ Both all-metal and PTFE heatbreak included） | 1 PC | |
| 18 | Electronics | 24V Heater Cartridge (slim wires) | 1 PC | |
| 19 | Electronics | Thermistor NTC 100K B3950 | 1 PC | |
| 20 | Electronics | VHB tape (20mm) | 1 PC | |
| 21 | Cables | VORON V0 UMBILICAL FRAME | 1 SET  | upgrade |
| 22 | Cables | UMBILICAL  cable Teflon | 20 PCS | upgrade |
| 23 | Cables | VORON V0 UMBILICAL TOOL HEAD | 1 SET  | upgrade |
| 24 | Cables | Voron 0.2 cables kit（All cables are connected to the terminals，Plug and play，Label buckle）Teflon wire | 1 SET  | |
| 25 | Cables | 2mmx120mm zip ties | 50 PCS | |
| 26 | Cables | Network cable | 1 PC | |
| 27 | Cables | Type-C line elbow | 1 PC | |
| 28 | Motion | F623-RS Bearing | 24 PCS | |
| 29 | Motion | MGN7H Linear Rail with Carriage (150mm) Stainless steel 440C | 5 PCS  | |
| 30 | Motion | GT2 20T (6mm wide) (5mm bore) | 2 PCS  | |
| 31 | Motion | 6RF Open Belt 6mm GT2 (2.1 meters) | 1 PC | |
| 32 | Motion | T8 flange Nut 8mm Lead --anti-backlash | 1 PC | |
| 33 | Buildplate | Aluminum Build Plate (MIC6) 120x120mm | 1 PC | Positionable steel plate like prusa |
| 34 | Buildplate | Silicone DC 24V Heater 100x100mm 75W （Faster heating rate）with plug | 1 PC | |
| 35 | Buildplate | Thermal Fuse (125C)  with plug | 1 PC | |
| 36 | Buildplate | Yellow die springs 8x4x20mm | 3 PCS  | |
| 37 | Buildplate | PEI Powder Coated Spring Steel Flex Buildplate 120x124mm  notched | 1 PC | |
| 38 | Buildplate | Magnetic sheet for spring steel plate 120x120mm | 1 PC | |
| 39 | Panels | Voron 0.2 Acrylic Panels kit | 1 SET  | |
| 40 | Bowden | Bowden Fitting ECAS04 | 2 PCS  | |
| 41 | Bowden | Bowden Tubing 4mmOD 1.9mmID (1.5 meter) | 1 PC | |
| 42 | Misc | Tank Chain 7x7mm | 1 PC | |
| 43 | Misc | Little Rubber Feet (14x11x11mm) | 4 PCS  | |
| 44 | Misc | XH2.54 2/3/4 Pin Plastic shell | 1 SET  | |
| 45 | Misc | 6mm x 3mm Round Neodymium Magnets | 8 PCS  | |
| 46 | Misc | Weaving casing φ8mm length 180mm | 1 SET  | |
| 47 | Misc | Weaving casing φ8mm length 205mm | 1 SET  | |
| 48 | Misc | FYSETC label | 1 PC | |
| 49 | Misc | Voron V0 Full Metal Heat Bed Frame | 1 PC | upgrade |
| 50 | Misc | Voron V0 Full metal gantry Super light CNC Part | 1 PC | upgrade |
| 51 | Misc | VORON V0  Rail retainer | 1 PC | upgrade |
| 52 | Misc | PVC wiring duct 160 | 1 PC | upgrade |
| 53 | Tools | Cutting pliers | 1 PC | |
| 54 | Tools | Hexagonal wrenchs | 1 SET  | |
| 55 | Misc | Thermal silica | 1 PC | |
| 56 | Misc | FYSETC Voron V0.2 Wiring manual | 1 SET  | |

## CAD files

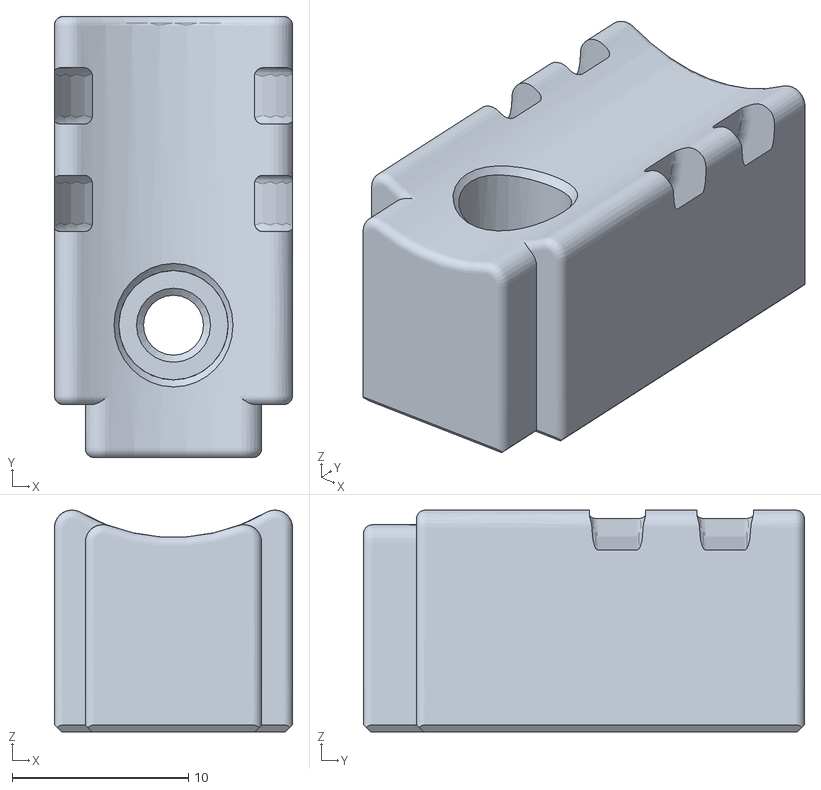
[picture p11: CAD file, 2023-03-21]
0.2/STL/[a]_Cable_Tie_x1.STL
13.5 x 25.0 x 12.6

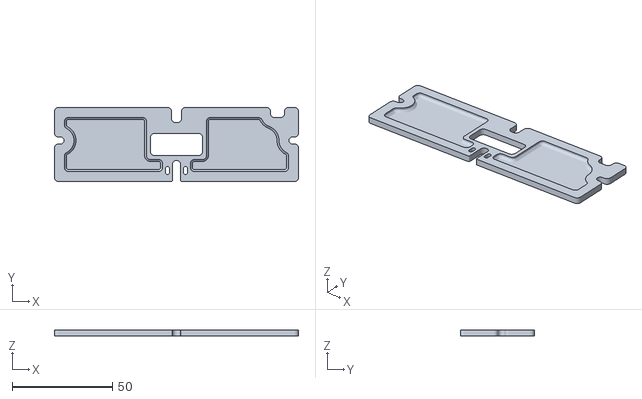
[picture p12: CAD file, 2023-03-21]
0.2/STL/ADD/FramePCBCover X1.STL
122.0 x 37.0 x 3.00

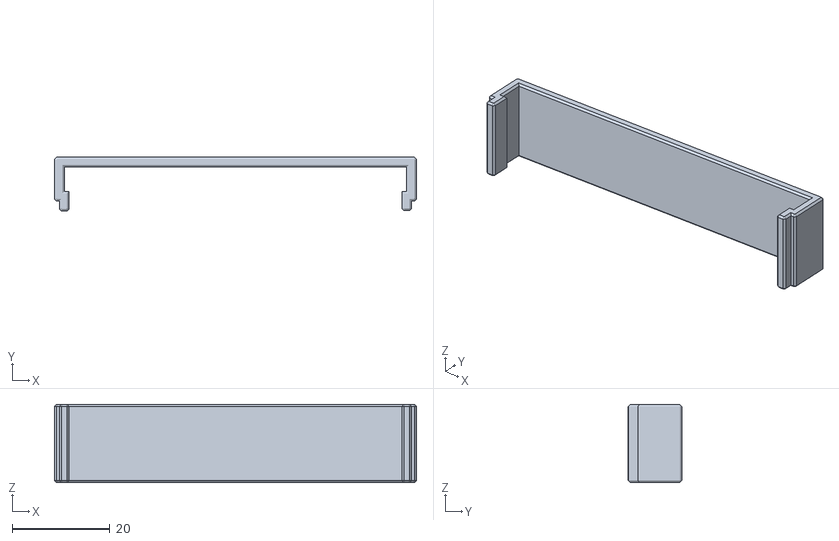
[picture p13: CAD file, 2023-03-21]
0.2/STL/Electronics/PSU_Cover_x1.STL
74.2 x 11.0 x 16.0

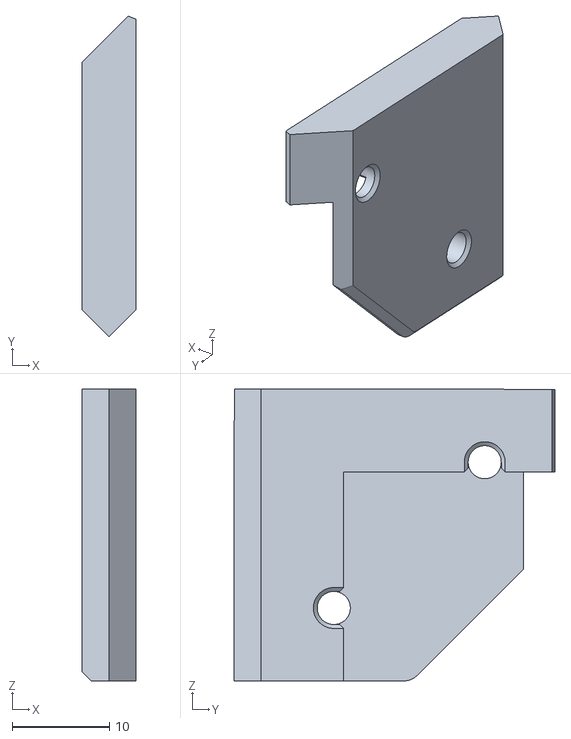
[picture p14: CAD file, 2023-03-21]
0.2/STL/Panel_Mounting/VHB panel clips/TH_Corner_Upper_1.stl
5.50 x 33.0 x 30.0

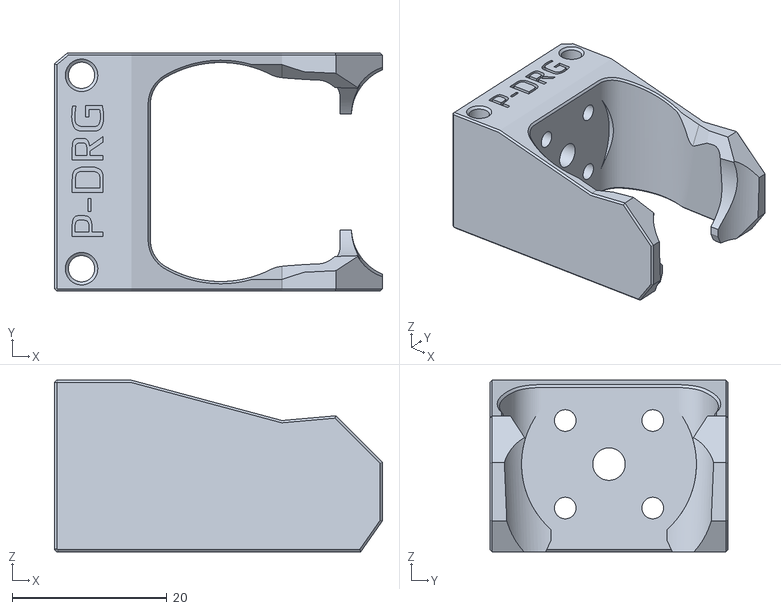
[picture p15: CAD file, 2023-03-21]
0.2/STL/Toolheads/Hotend_Mounts/Fan_Saver/FS_Hotend_Mount_Dragon.stl
42.4 x 30.8 x 22.2

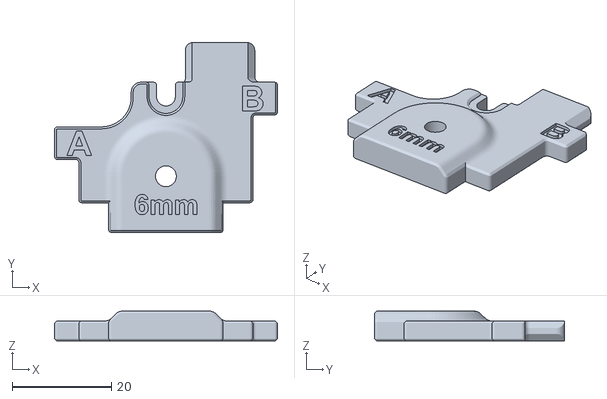
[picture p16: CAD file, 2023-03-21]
0.2/STL/Tools/Pulley_Jig_V02.stl
44.9 x 38.3 x 6.00

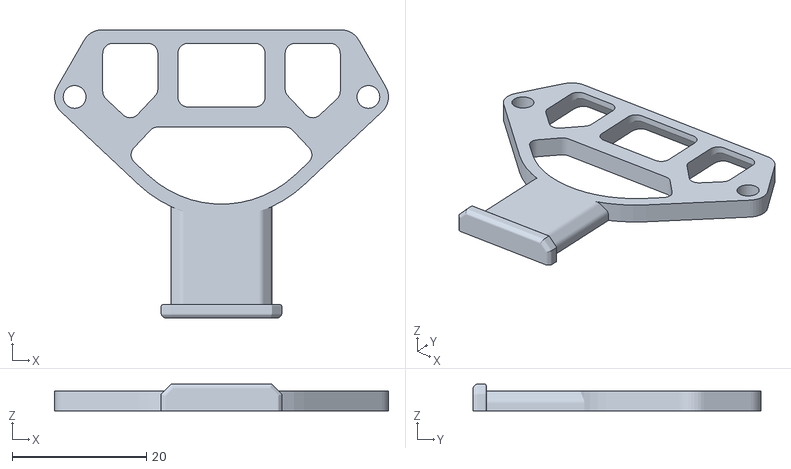
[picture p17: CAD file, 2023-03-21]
0.2/STL/ADD/ToolheadSpacer_with_StrainRelief X1.STL
49.8 x 43.0 x 4.00

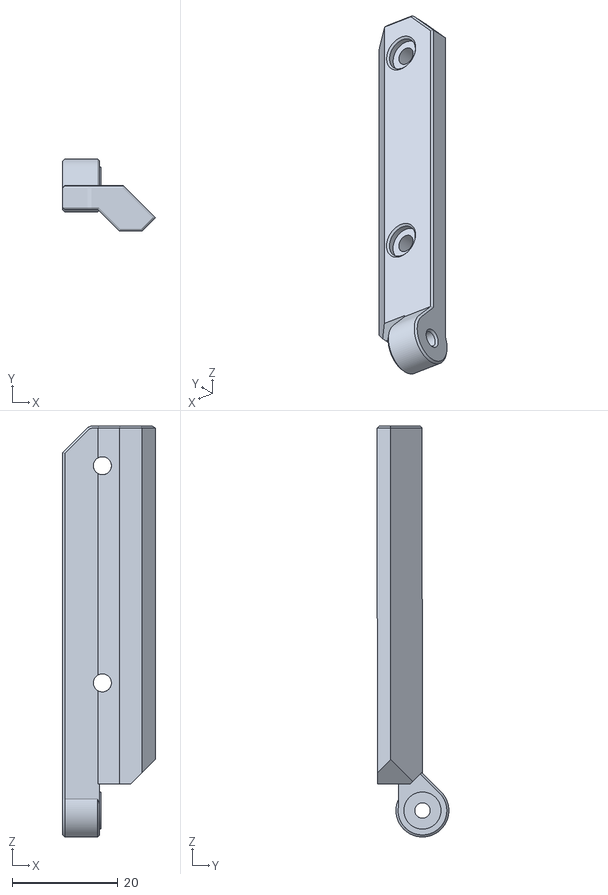
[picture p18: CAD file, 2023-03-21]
0.2/STL/Panel_Mounting/VHB panel clips/MirrorHinge_A_Bottom.stl
17.5 x 13.6 x 77.6

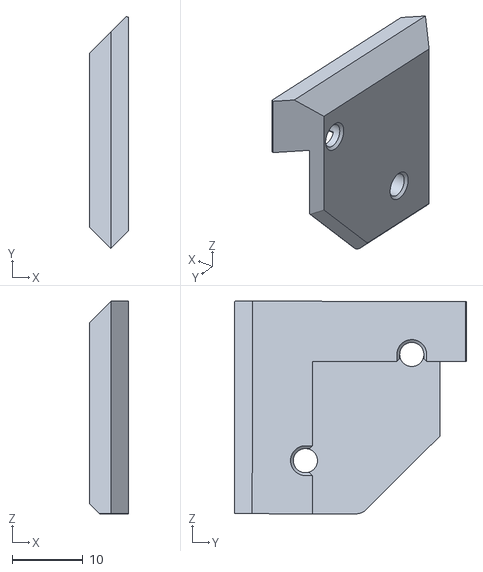
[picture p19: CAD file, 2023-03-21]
0.2/STL/Panel_Mounting/VHB panel clips/BL_Corner_Bracket.stl
5.50 x 32.7 x 30.0

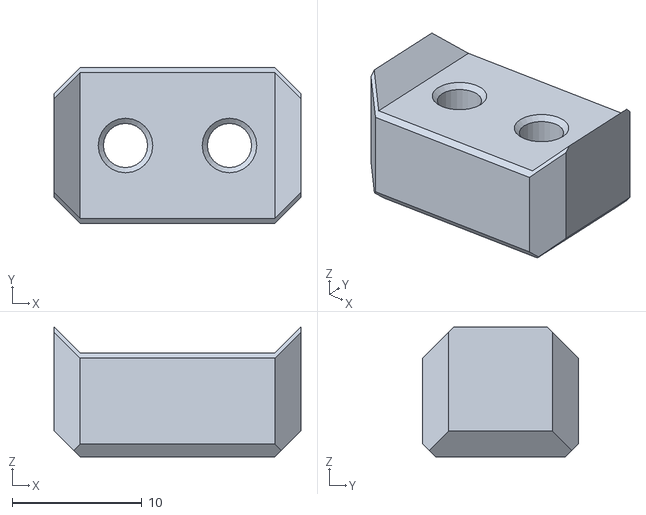
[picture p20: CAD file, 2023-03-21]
0.2/STL/Drag_Chain_Spacer_x1.stl
19.0 x 12.0 x 10.0

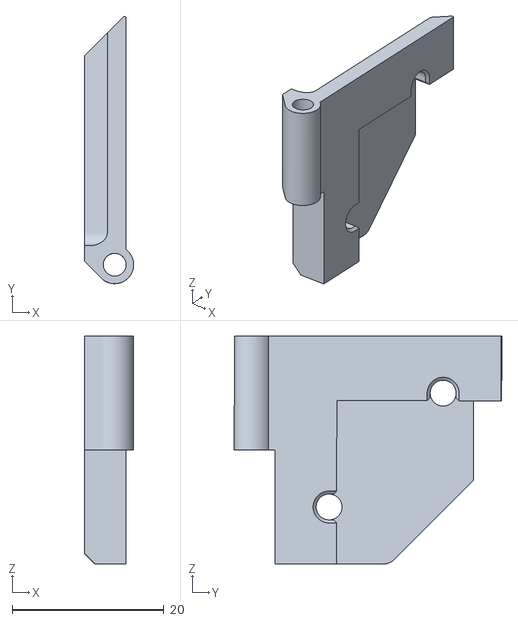
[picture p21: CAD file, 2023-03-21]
0.2/STL/Panel_Mounting/VHB panel clips/right_btm_front_hinge.stl
6.50 x 35.2 x 30.0

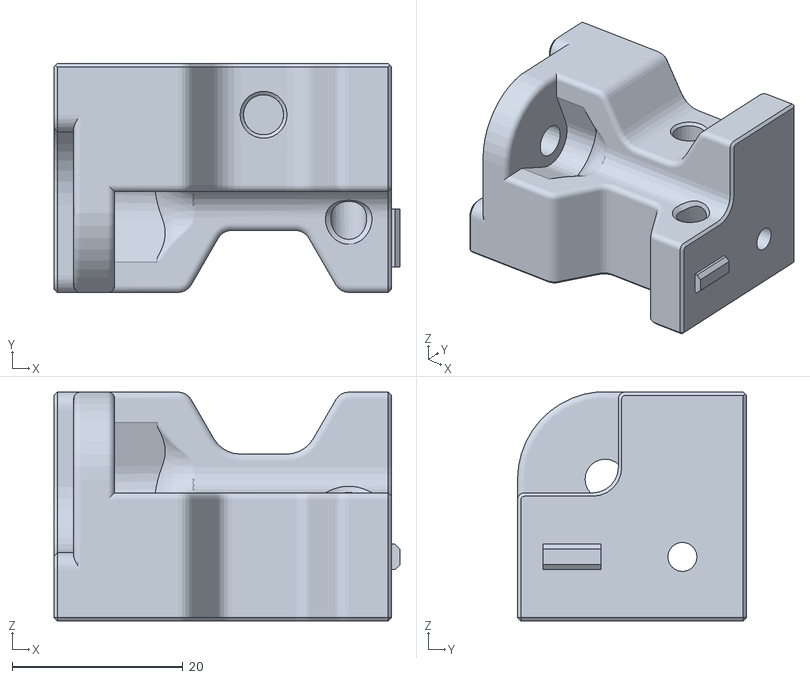
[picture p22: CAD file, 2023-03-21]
0.2/STL/Skirts/Foot_Rear_Right_x1.stl
40.5 x 26.8 x 26.8

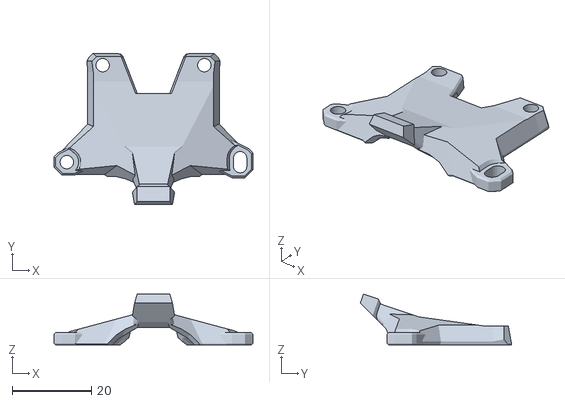
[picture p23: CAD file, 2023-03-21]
0.2/STL/Toolheads/Mini_Stealthburner/Strain_Relief_Body_x1.stl
50.3 x 38.3 x 12.9

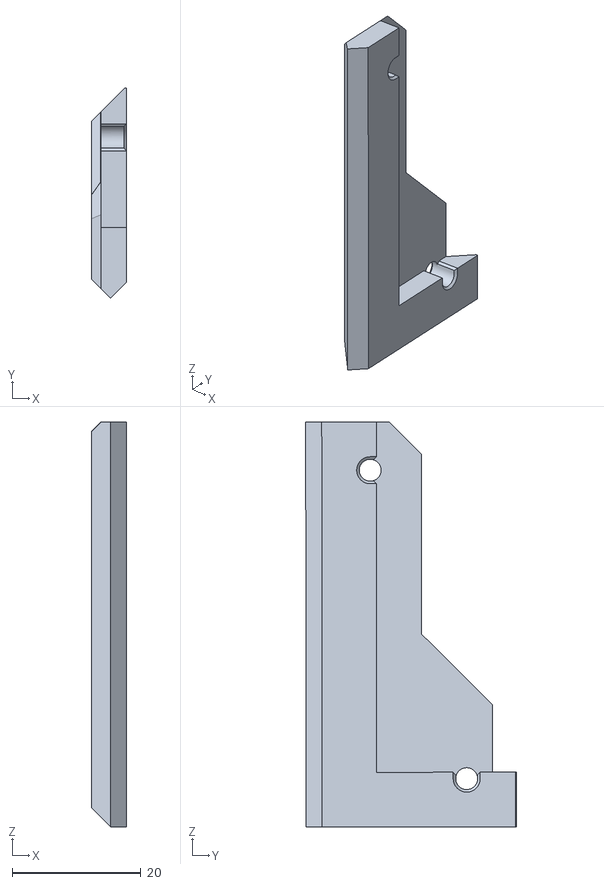
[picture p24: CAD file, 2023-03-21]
0.2/STL/Panel_Mounting/VHB panel clips/left_top_Rear_clip2.stl
5.50 x 32.8 x 63.0

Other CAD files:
0.2/STL/Panel_Mounting/VHB panel clips/Hinge_A_bottom.stl
0.2/STL/Rear_Bed_Mount_Left_x1.stl
0.2/STL/Panel_Mounting/VHB panel clips/TH_Corner_Lower_1.stl
0.2/STL/Panel_Mounting/VHB panel clips/left_top_front_clip2.stl
0.2 R1 V1.1/STL/ADD/Bed_Wago_Mount_x1.STL
0.2 R1 V1.1/STL/ADD/Drag_Chain_Spacer_x1.STL
0.2 R1 V1.1/STL/ADD/Fan_Mount_x1.stl
0.2 R1 V1.1/STL/ADD/Gantry_Mount_x2.stl
0.2 R1 V1.1/STL/ADD/Harness_buckle_x6.STL
0.2 R1 V1.1/STL/ADD/Tool_board_cover_B_x1 PETG.STL
0.2 R1 V1.1/STL/A_Drive_Frame_Lower_x1.stl
0.2 R1 V1.1/STL/A_Drive_Frame_Upper_Rev1_x1.STL
0.2 R1 V1.1/STL/A_Idler_Lower_x1.stl
0.2 R1 V1.1/STL/A_Idler_Upper_x1.stl
0.2 R1 V1.1/STL/B_Drive_Frame_Lower_x1.stl
0.2 R1 V1.1/STL/B_Drive_Frame_Upper_Rev1_x1.STL
0.2 R1 V1.1/STL/B_Idler_Lower_x1.stl
0.2 R1 V1.1/STL/B_Idler_Upper_x1.stl
0.2 R1 V1.1/STL/Display/Display_Knob_x1.stl
0.2 R1 V1.1/STL/Display/Display_Mount_Left_x1.stl
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

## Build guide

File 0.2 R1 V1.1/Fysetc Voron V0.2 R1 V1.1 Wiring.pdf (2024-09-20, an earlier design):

LED
+V

ADJ.

### Z-MOTOR

### B-MOTOR

### A-MOTOR

### Voron V0 Display

HOT SURFACE
DO NOT TOUCH

### E-MOTOR

5A

LED

SR | Z-stop

### FAN2

USB

ETH

HE

TE

# FYSETC VORON 0.2 R1 PRO V1.1 wiring

Please select the voltage of your area before powering up.

230V | 115V

Before you perform the wiring, please check whether your accessories are intact, especially to confirm that all cables are intact. After connecting, please check whether the wiring position is correct. If you have a multimeter, it is best to use the multimeter to check whether there is a short circuit in each power supply position, especially the position of the switching power supply.

Please be sure to check before powering on. If there is an abnormal situation, please cut off the power immediately and perform the inspection again. Please always pay attention to safety.

SR
Z

TB

HB

HB

V1
V2

FAN2

HB
HB

TB

Wago

Wago

### FAN0

### FAN1

### FAN0

### RGB

### RGB

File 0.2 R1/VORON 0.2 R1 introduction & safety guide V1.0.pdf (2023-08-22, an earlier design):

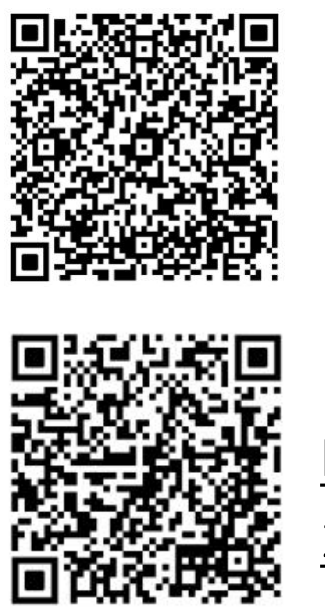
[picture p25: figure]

V1.0 | Powered by VoronDesign, Produce by FYSETC | www.fysetc.com

# Product Introduction

Thank you for purchasing Voron 3D printer kit from FYSETC. This kit is based on VORON Official V0.2 R1 (no printed

parts included).

In case of any printer-related problem, do not hesitate to contact our customer service. We are glad to receive all of your valuable comments and tips. More product info here: https://github.com/FYSETC/FYSETC-Voron-0.2-Pro

# Product details

Mechanical structure:
- Frame: aluminum box structure
- Printing platform: mic6 thickened aluminum
- Plate: elastic powder steel plate
Print parameters:
- Printing technology: FDM
- Build volume: 120x120x120mm
- Printing layer height: 0.05-0.3mm (use 0.4mm nozzle)
- Maximum printing speed: 200mm/s (recommended: 20-80mm /s)
- Filament diameter: 1.75mm
- Nozzle diameter: 0.4mm
- Filament types: PLA, ABS,PETG, PLA-CF carbon fiber, TPU, HIPS, WOOD, etc. Temperature:
- Maximum extruder temperature: 260°C (higher if metal heat break used)
- Maximum temperature of hot bed: 120°C
Software parameters:
- Firmware: Klipper
- Supported formats: STL, G-code, AMF, OBJ
- Input mode: Ethernet, WiFi
- Operating software: Simplify3d, PrusaSlicer, Cura, Repeater host
- Operating system: Windows 7/ Mac OS / Linux Hardware parameters:
- WiFi: support (Based on Raspberry Pi)
- Controller : Cheetah(2209x4) + Raspberry Pi 3/4
- Display: 1.3 inch OLED Display Screen
- Power supply: Meanwell LRS-150-24
- Input: 100-120V,3.0A / 200-240V, 1.7A
Size & weight:
- Machine size: 240x242x382mm
- Package size: 465x305x175mm
- Net weight of machine: 6kg

# Disclaimer

Failure to read the assembly descriptions may lead to personal injury, inferior results, or damage to the 3D printer. Always ensure that anyone who operates the 3D printer

knows and understands the operation description. We cannot control the conditions in which you assemble the kit. For this, and other reasons, we do not assume

responsibility, and expressly disclaim liability for loss, injuries, damage, or expense arising out of, or in any way connected with, the assembly, handling, storage, use or disposal of the product. The information in this handbook is provided without any warranty, expressed or implied, regarding its correctness. Licenses

VORON 0.2 printer is a part of the VoronDesign project, the first open-source 3D printer project free to use under a
GNU | General | Public | License | v3.0 | license
(www.gnu.org/licenses/gpl-3.0.en.html). Permissions: Commercial use, Modification, Distribution, Patent use, Private use

Limitations: Liability, Warranty

You can download the print parts at. https://github.com/FYSETC/FYSETC-Voron-0. 2-Pro/tree/main/0.2%20R1/STL

FYSETC Voron 0.2 Pro database knowledge. https://github.com/FYSETC/FYSETC-Voron-0. 2-Pro

Follow the manual below to assemble the kit. https://github.com/VoronDesign/Voron-0/tre

e/Voron0.2r1/Manuals

V1.0 | Powered by VoronDesign, Produce by FYSETC | www.fysetc.com

# Safety Guide

Read and understand the assembly manual and safety instructions before beginning to assemble and use the kit. Failure to do so may result in serious injury or death. Save this document. Please be very cautious during any interaction with the

printer. This printer is an electrical device with moving parts and hot-temperature areas. Assembly

- Never disassemble the printer's power supply: it does not contain any parts that can be - repaired by unskilled workers. All repairs must be carried out by qualified technicians. ● In the process of assembling and using the printer, please be careful not to touch or go deep into the

moving position to avoid scratching or pinching. ● Adult supervision required: Prevent children from

touching printer parts or printers unattended, even if the printer is not assembled or printed. Observe children closely and intervene if necessary to prevent potential safety issues and ensure proper use of the printer. Ensure that young children cannot touch small 3D printed parts or 3D printed parts. These are potential suffocation hazards for young children. Wiring

- Before starting the wiring, please read the wiring diagram carefully, understand the installation method of each position, confirm the positive and negative positions, especially confirm that the AC wiring of the PSU is correct and there is no short circuit. The inspection is to observe the wiring position instead of just looking at the color. ● Please make sure that all electronic wires are not

damaged mechanically or otherwise. If so, please stop using the damaged electronic wire immediately and replace it. ● Before powering on for the first time, please make

sure that you have selected the input voltage of the PSU according to your area, otherwise the PSU will be severely burned, or even other peripherals such as the motherboard, and cannot be repaired. Use

- The printer is for indoor use only. Do not expose the printer to rain or snow. Always place the printer in a dry environment and keep at least 30 cm away from other objects. ● Always place the printer in a stable place to prevent it

from falling or tipping over. ● After the machine is debugged, you must be on duty

throughout the printing process to avoid malfunctions. In several cases, it may cause a fire. Please do not leave the printer unattended when the printer is turned on!

- When you unplug the power cord from the socket, pull the plug instead of the power cord to reduce the

risk of damaging the plug or AC power outlet. ● During the process of setting up and operating the

printer, the printing platform and the printing nozzle are at a high temperature. Avoid direct contact with these areas. The nozzle temperature is 190-260°C (374-500°F); the heating bed temperature can reach above 100 °C (212 °F). Temperatures higher than 40 °C (104 °F) can cause harm to the human body. ● The plastic melts during the printing process and

produces a peculiar smell. Put the printer in a well-ventilated place. Manual:

https://github.com/VoronDesign/Voron- 0/raw/Voron0.1/Manuals/Assembly_Man

ual_0.1.pdf

CNC Parts Buy Link:
https://www.aliexpress.com/item/10050 02212789450.html

Print Parts Link:
https://www.thingiverse.com/thing:49141 52

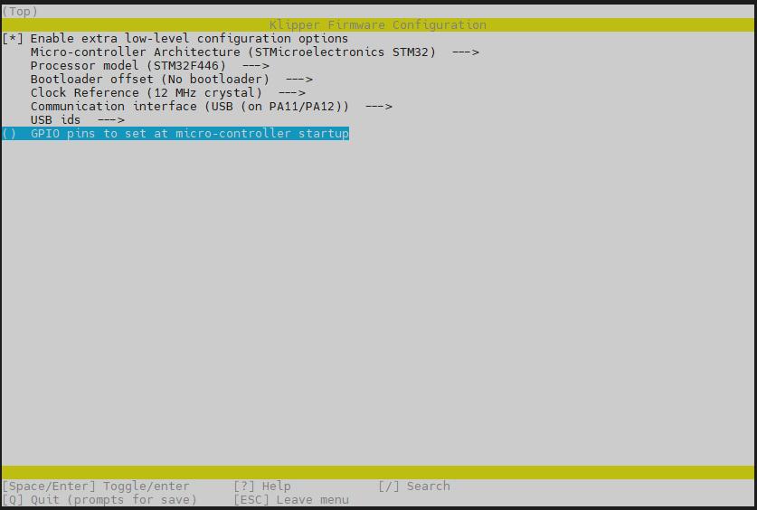
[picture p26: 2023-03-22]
0.2/Firmware&OS/makemenuconfig.jpg

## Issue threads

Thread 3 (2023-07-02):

Bad sense_resistor value in printer.cfg + Cheetah 3.0

n00xt, 2023-07-02:
There is a bad value for sense_resistance in repository printer.cfg with Cheetah 3.0 board.

https://github.com/FYSETC/FYSETC-Voron-0.2-Pro/blob/main/Firmware%26OS/printer.cfg

Good value is 0.220

gihad, 2023-07-02:
Thsi value appears 4 times since there are multiple sensors. Which one is incorrect?

n00xt, 2023-07-02:
Steppers section value of sense_resistor: 0.110

gihad, 2023-07-02:
Can you clarify which of the 4 steppers?

n00xt, 2023-07-02:
This one working for me.

https://github.com/FYSETC/Cheetah_V3.0/blob/main/Software/Cheetah%20V3%20-%20Fsyetc%20V0.2.cfg

quarkvalk, 2023-10-21:
https://github.com/FYSETC/FYSETC-Voron-0/issues/3#issuecomment-1721966282

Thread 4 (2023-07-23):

Tophat lower clips are oriented upside down

microkc, 2023-07-23:
The following 2 parts are oriented with the wrong face on the build plate.

TH_Lower_Clip_Mirror_x3.stl
TH_Lower_Clip_x3.stl

They are located in 0.2/STL/Tophat.  The parts in the 0.2r1 folder are already correct.

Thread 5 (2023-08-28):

voron 0.2 r1 pro updating mistakes...

kramerjunior, 2023-08-28:
Hello, i'm French i'm a new owner of a beauty Voron 0.2 r1 pro from AE...
When i finally finish my build i make the Great Update from the interface....
then.....
[moonraker(1).log](https://github.com/FYSETC/FYSETC-Voron-0.2-Pro/files/12458183/moonraker.1.log)
[klippy(1).log](https://github.com/FYSETC/FYSETC-Voron-0.2-Pro/files/12458184/klippy.1.log)
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

Could you help me to find an issue?
thank you all.

shoikan, 2023-09-01:
It appears the instructions are a bit incorrect. They clearly and explicitly state to use a 12MHz crystal which does not appear to work, however I found that if you use the 8MHz option it does work. YMMV of course.

kramerjunior, 2023-09-04:
it's the same problem with 8mhz... do you have an other idea ???

shoikan, 2023-09-05:
No, unfortunately no idea. On top of the issue with the wrong crystal speed, my whole board seems to have given up the ghost since it no longer accurately reports temperatures all of a sudden. Can't test more things for you anymore since it's no longer built into my voron and will soon make it's way into the trash-bin if Fysetc keeps ignoring their support email box. Thoroughly disappointed with this board. Waste of $75-125 that I'd rather have spent on a board that keeps working.

runningsystemchanger, 2024-11-07:
Check the instructions here: https://github.com/FYSETC/Catalyst_Kit_V2.0
The CATALYST 2.0 has STM32F446. Not 401.

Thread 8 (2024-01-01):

unable to obtain Root access to Catalyst Board, wifi connection issues

violinbf, 2024-01-01:
Hello, I am trying to configure wifi with the latest Debian 11 version of the Catalyst firmware on your Github repository ( file name: cm68-debian11-voron02pro-part-20231215.rar ) . These instructions provided on the github to not initialize the wifi. (note: I have removed my actual ssid and password from these lines) here is what comes back:

_________________________________
linaro@voron-02-pro:~$ sudo wifi_sta_start.sh ssid password
sudo: unable to resolve host voron-02-pro: Name or service not known
sudo: wifi_sta_start.sh: command not found
linaro@voron-02-pro:~$
_____________________________________

after manually connecting to my router through the command line, I tried to run your instructions for configuring wifi on boot but get this message

____________________________________
linaro@voron-02-pro:~$auto wlan0
iface wlan0 inet dhcp
wpa-ssid ssid
wpa-psk password
-bash: linaro@voron-02-pro:~$: command not found
-bash: sudo:: command not found
-bash: sudo:: command not found
-bash: linaro@voron-02-pro:~: command not found
-bash: iface: command not found
-bash: wpa-ssid: command not found
-bash: wpa-psk: command not found
________________________________________

I am able to initialize wifi connection and ip address through the command line, but in order to run on boot I need to make changes to the wpa_supplicant.service I need root access.

I am unable to obtain root access by using the usr: root pwd: root. Can you please provide the correct root access information for this most currentfirmware?

Do you have a simple way of configuring wifi on boot with the most current firmware? if so can you provide instruction?

Thank you

b-dealmeida, 2024-11-30:
The default username and password for my Catalyst was linaro

Duckferd, 2025-01-14:
@violinbf were you ever able to resolve this error? I'm on the verge of just reflashing to an earlier firmware because I'm having the exact same issues with sudo not registering and being unable to add the host name to the host list.

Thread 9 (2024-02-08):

Power Inlet STL for CNC Foot missing

ensoniq2k, 2024-02-08:
Hi,

I bought the CNC kit and I can't find a printable power inlet STL where the CNC machined foot is spared out.

I could only find Foot_Rear_Left_Inlet_x1.STL which includes the foot-part.

Did I just overlook it or is the file actually missing?

Thanks
Sascha

ensoniq2k, 2024-02-09:
I found it in Siboors Github repo if anyone is wondering:

https://github.com/Lzhikai/SIBOOR-Voron-0.2/blob/main/Metalsupplements/Skirts/Foot_Rear_Left_Inlet_x1.stl

leo-na-rd, 2025-06-08:
don't listen to @ensoniq2k, it's not gonna fit. Ask me how I know.

Instead, print this:
https://www.printables.com/model/746838-fysetc-voron-02-pro-r1-cnc-kit-main-inlet-cutout/files

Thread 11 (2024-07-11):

Erro de dimensionamento de peças

gfBarreto, 2024-07-11:
Alguns problemas consegui sanar com a ajuda de um amigo que montou uma dias antes de mim. Não tenho experiência nesta área, pois é a primeira voron que monto.
Estou tendo problema de dimensionamento das peças...
Exemplo, antes as peças saiam como se estivesse a mesa torta e tbm com erro de dimensões.
Conforme fui ajustando as correias teve uma leve melhorada, agora parecem sair no local estipulado, porém ainda com erro de dimensionamento.
Abri chamado no Ali, com esperança de receber suporte mas acabou que foi aceito o reembolso e tenho até dia 02/08 para enviar a impressora, mas não é esta a minha vontade. Quero tentar solucionar.

As correias estão tão frouxas que embarrigam ao serem tracionadas, foi a única forma de conseguir imprimir perto do ideal.

Não sei se algum problema mecânico, motor, configuração.

Alguém pode dar uma luz???
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

ejhoness, 2024-09-21:
olá, posta um log, klipper.log para eu ver. tem opção rollover para fazer um log pequeno e novo.
acredito que as correias bambas, frouxas, devam contribuir para erros de dimencionamento, acredito que deva ter que ajustar nas configurações printer.cfg o " tamanho do movimento do motor"  as peças estarem saindo tortas pode ser que quando prendeu as correias o carro Y ficou desalinhado, verifique se ele encosta em ambos os lados x no final e no inicio de y. são apenas algumas observações, não entendi pela fotos a dimensão que mandou imprimir, poderia detalhar. antes tarde que nunca. mande umas fotos da sua impressora, e me conte como está. do mais lhe desejo vida longa e prospera.

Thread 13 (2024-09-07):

Missing steel parts

Ramay71, 2024-09-07:
I bought this 0.2 R1 V1.1 and I start to assemble...
Crazy manual, always on loop...
Some printed parts missing too but I printed again...
When I reached page 134 I just stopped everything to try to find this "M3 MARKERBEAM XL" NUTS, I opened every single package trying to find this and nothing, I have no simple solution for this,
Some parts of this manual are incorrect with the actual parts on package.
Some one with some grear idea for this missing NUTS???
Thanks

ejhoness, 2024-09-21:
Hello, my friend,
You are well advanced in the assembly, I am still admiring the parts, tell me more about your assembly. In my kit this part is present, this is a metal piece 4.9 x 14.9 x 1.8 mm m3 thread in the center "M3 t-nut"

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

I think a yellow is missing

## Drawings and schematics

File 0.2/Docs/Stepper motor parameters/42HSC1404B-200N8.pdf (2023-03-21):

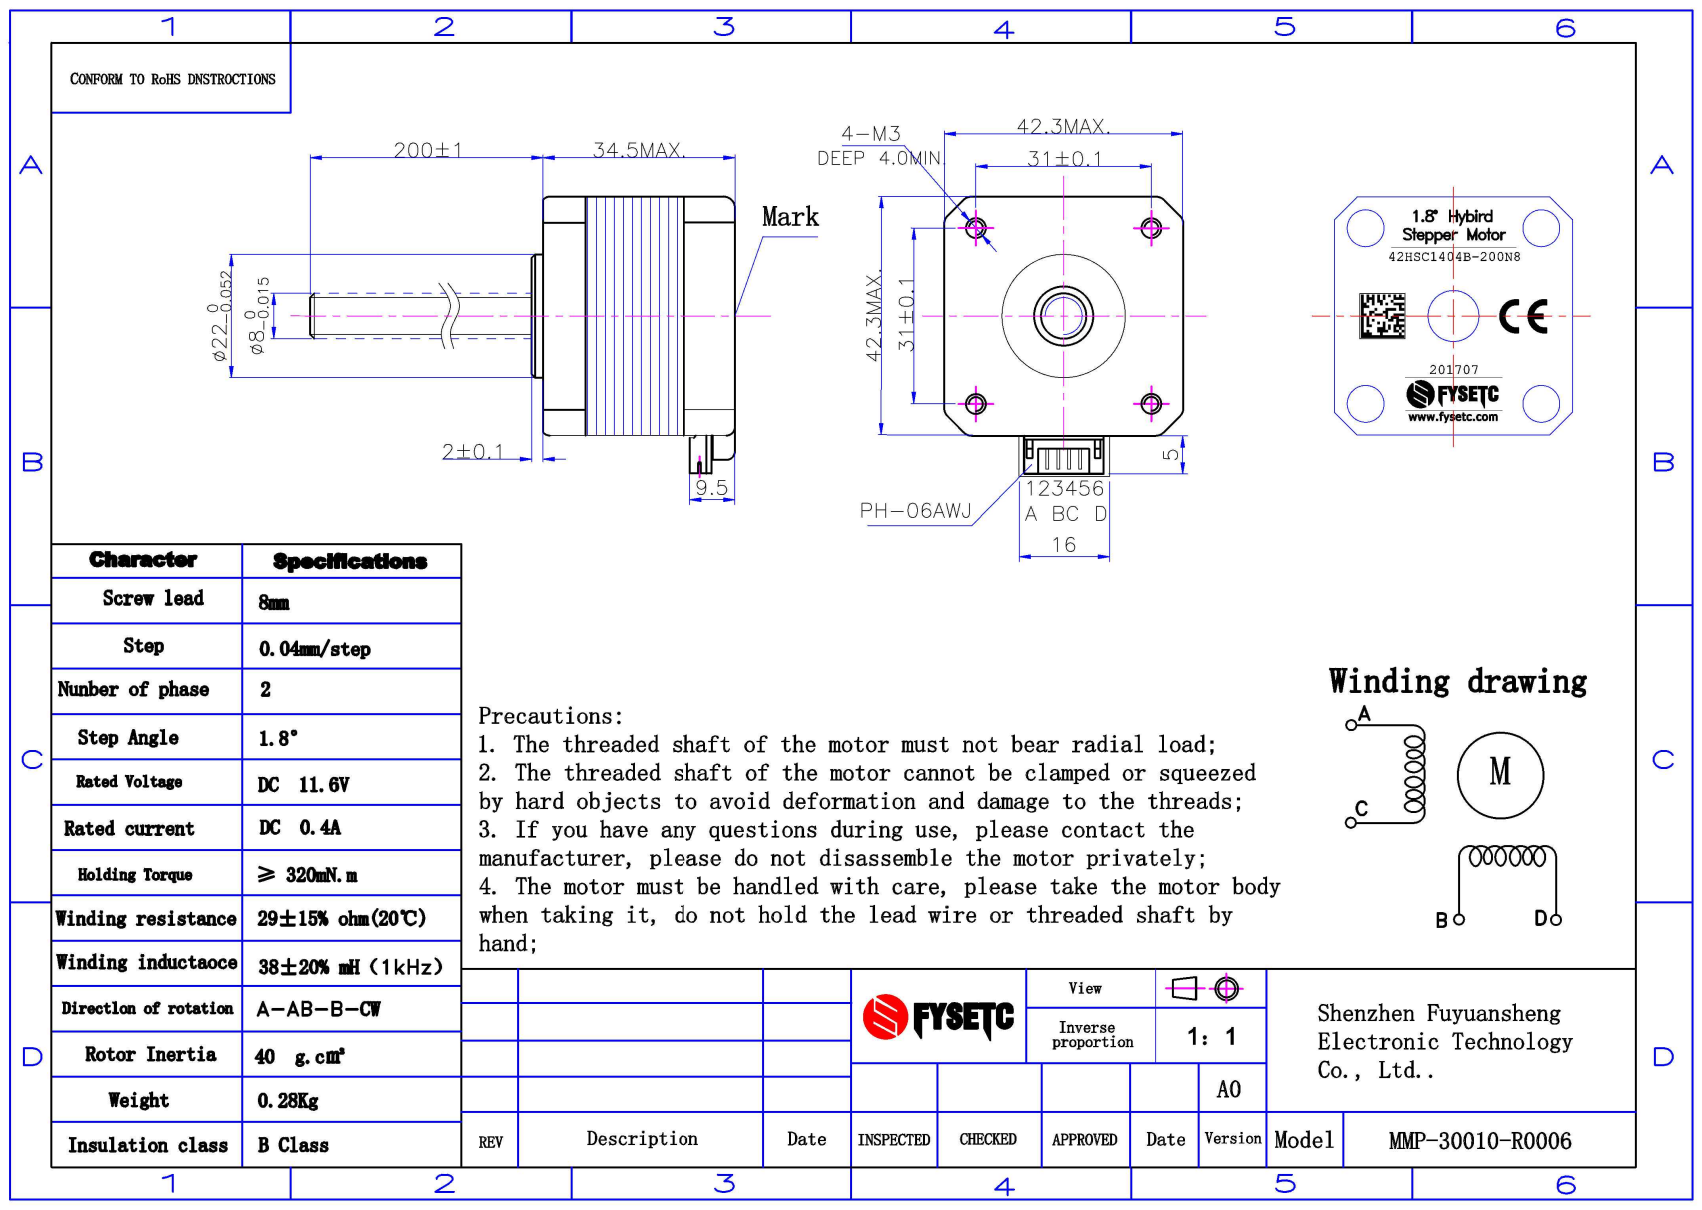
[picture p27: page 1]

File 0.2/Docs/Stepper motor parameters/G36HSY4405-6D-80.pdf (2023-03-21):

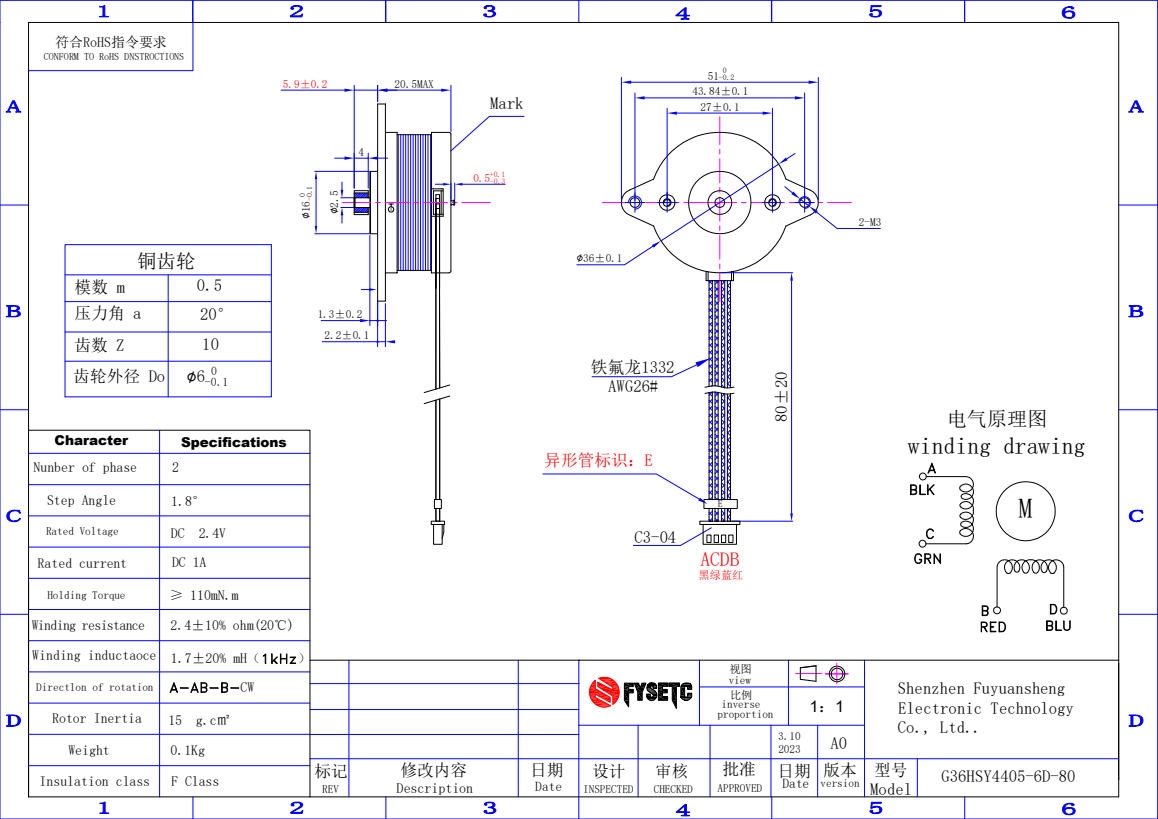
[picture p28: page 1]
电气原理图 1：1 视图; 修改内容; winding drawing; REV; Description; INSPECTED; CHECKED; APPROVED; Model Date Date; view; inverse proportion; version; 20.5MAX; Mark ∅; 铁氟龙1332 AWG26#; 铜齿轮; 压力角 a; 齿轮外径 Do; ACDB; 黑绿蓝红; 异形管标识：E; G36HSY4405-6D-80; Shenzhen Fuyuansheng Electronic Technology Co., Ltd..; 2.4±10% ohm(20℃); F Class Character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

符合RoHS指令要求
CONFORM TO RoHS DNSTROCTIONS

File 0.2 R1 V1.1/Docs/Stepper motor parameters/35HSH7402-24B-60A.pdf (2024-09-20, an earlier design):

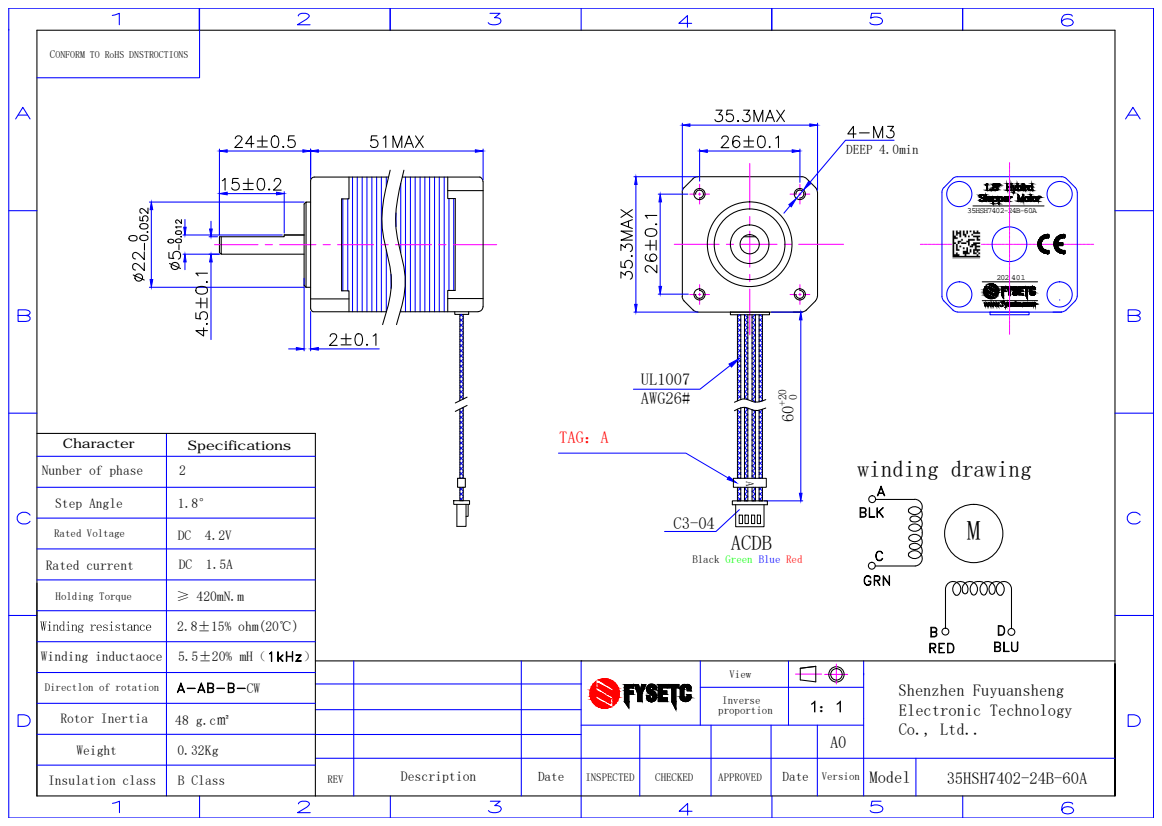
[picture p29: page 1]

0 UL1007 AWG26#C3-04 7$*$ A 0.32Kg 48 g.c e fRKP 2 DC 4.2V DC 1.5A f P+  P1P CW B Class 35HSH7402-24B-60A 202 401

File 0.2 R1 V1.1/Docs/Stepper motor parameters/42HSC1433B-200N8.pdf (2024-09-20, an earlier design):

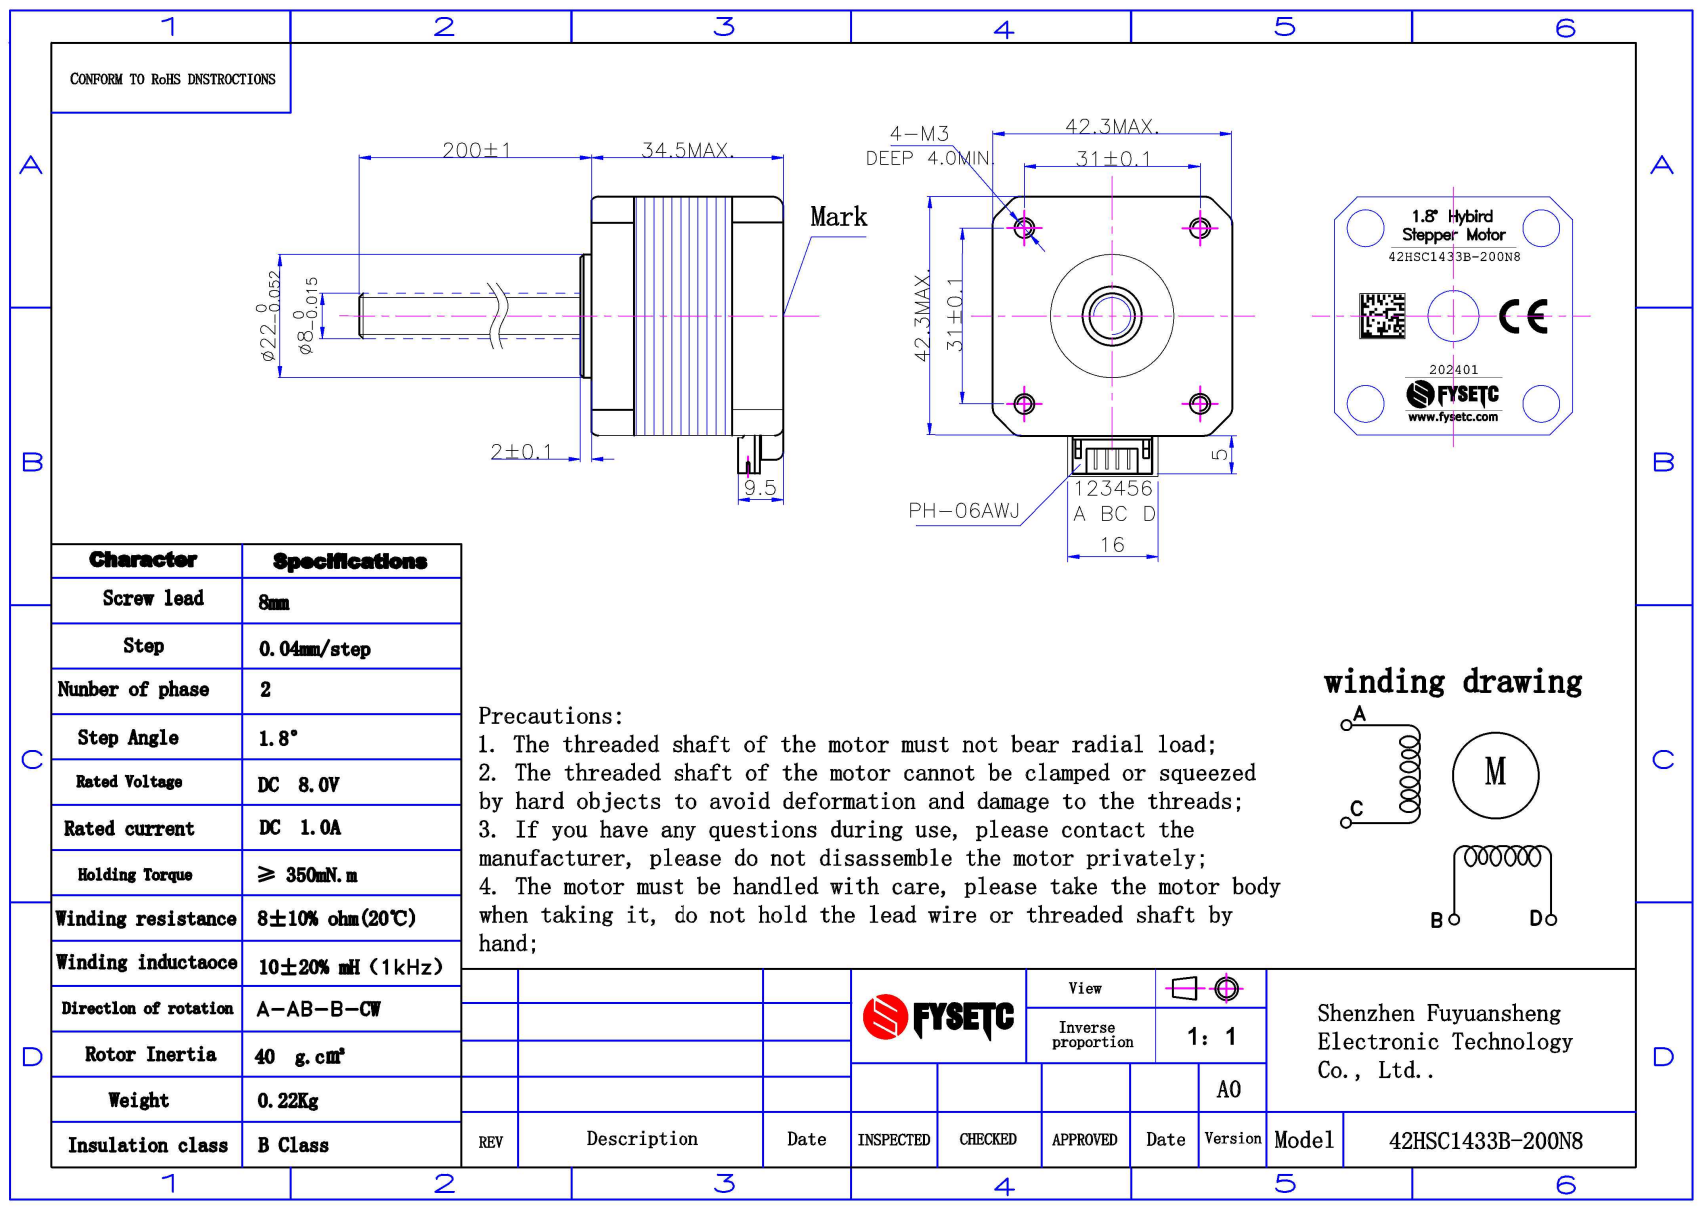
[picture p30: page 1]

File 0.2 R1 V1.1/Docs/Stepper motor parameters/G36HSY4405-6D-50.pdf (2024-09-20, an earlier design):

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

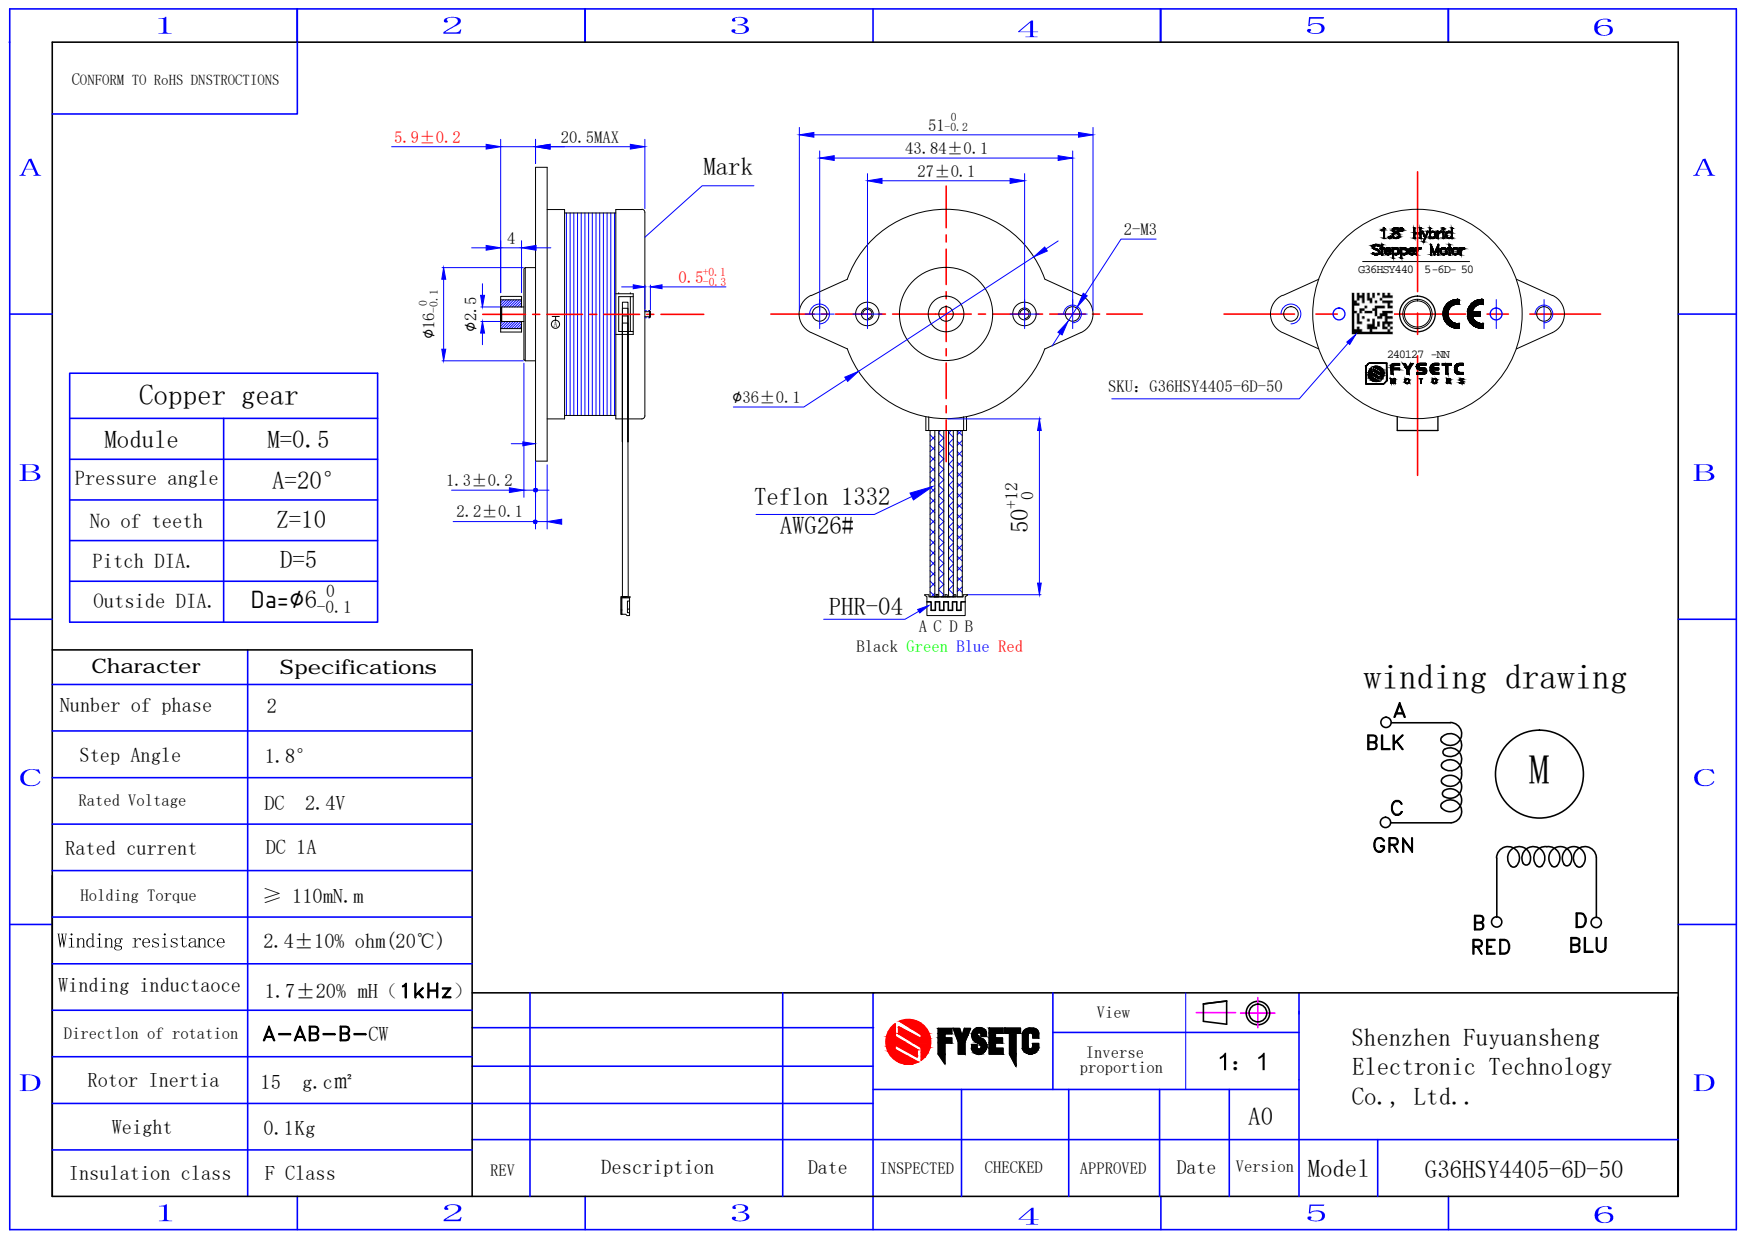
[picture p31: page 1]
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

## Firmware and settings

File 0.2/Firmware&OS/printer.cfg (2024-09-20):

# This file contains common pin mappings for the Fysetc Cheetah v3.0
# board. To use this config, the firmware should be compiled for the
# STM32F446 with "No bootloader" and Communication interface USB

# After running "make", run the following command to flash the board:
# dfu-util -R -a 0 -s 0x08000000:leave -D out/klipper.bin
# or
# make flash FLASH_DEVICE=0483:df11 

## Voron Design VORON 0.2 FYSETC Cheetah 3.0 config

## *** THINGS TO CHANGE/CHECK: ***
## MCU path                                                                     [mcu] section
## Z and Extruder motor currents                                                [tmc2209 stepper_*] sections. Uncomment the stepper motor you have
## Full steps per rotation for Extruder                                         [extruder] section
## Thermistor types                                                             [extruder] and [heater_bed] sections - See https://www.klipper3d.org/Config_Reference.html#common-thermistors for common thermistor types
## Extruder motor currents                                                      [extruder] section
## PID tune                                                                     [extruder] and [heater_bed] sections
## Fine tune E steps                                                            [extruder] section

## For more info                                                                check https://docs.vorondesign.com/build/startup/#v0
# See docs/Config_Reference.md for a description of parameters.

[include mainsail.cfg]

[mcu]
#####################################################################
# Obtain definition by "ls -l /dev/serial/by-id/"
#####################################################################
serial: /dev/serial/by-id/usb-Klipper_stm32f446xx_2C001B000950535858343820-if00
# serial: /dev/ttyAMA0   # for UART connection
# baud: 250000
# restart_method: command
[temperature_sensor mcu_temp]
sensor_type: temperature_mcu
min_temp: 0
max_temp: 100

[temperature_sensor raspberry_pi]
sensor_type: temperature_host
min_temp: 10
max_temp: 100

[printer]
kinematics: corexy
max_velocity: 200
max_accel: 3000
max_z_velocity: 15
max_z_accel: 45
square_corner_velocity: 6.0

#####################################################################
#      X/Y Stepper Settings
#####################################################################
[stepper_x]
step_pin: PC0
## Refer to https://docs.vorondesign.com/build/startup/#v0
dir_pin: PC1                                                       # Check motor direction in link above. If inverted, remove ! before PC1
enable_pin: !PC3
rotation_distance: 40
microsteps: 32
full_steps_per_rotation: 200                                        # Set to 400 for 0.9�?degree stepper motor, 200 is for 1.8�?stepper motors
#endstop_pin: ^PA2
endstop_pin: tmc2209_stepper_x:virtual_endstop
position_endstop: 120
position_max: 120
homing_speed: 40                                                    # for sensorless homing it is recommended not to go above 40mm/s   
homing_retract_dist: 0
homing_positive_dir: true

[tmc2209 stepper_x]
uart_pin: PB3
#tx_pin: PA2
uart_address: 0
interpolate: False
run_current: 0.7
sense_resistor: 0.220
stealthchop_threshold: 0                                            # Set to 999999 to turn stealthchop on, and 0 to use spreadcycle
diag_pin: ^PA2                                                      # YOU NEED TO JUMP THIS DIAG PIN ON YOUR BOARD FOR SENSORLESS HOMING TO WORK 
driver_SGTHRS: 100                                                  # this is set to 255 which is the MAX sensitivity for sensorless homing, you will need to tune this later

[stepper_y]
step_pin: PC14
## Refer to https://docs.vorondesign.com/build/startup/#v0
dir_pin: PC13                                                      # Check motor direction in link above. If inverted, remove ! before PC13
enable_pin: !PC15
rotation_distance: 40
microsteps: 32
full_steps_per_rotation: 200                                        # Set to 400 for 0.9 degree stepper motor, 200 is for 1.8 degree stepper motors
#endstop_pin: ^PA3
endstop_pin: tmc2209_stepper_y:virtual_endstop
position_endstop: 120
position_max: 120
homing_speed: 40                                                    # for sensorless homing it is recommended not to go above 40mm/s   
homing_retract_dist: 0
homing_positive_dir: true

[tmc2209 stepper_y]
uart_pin: PB3
#tx_pin: PA2
uart_address: 1
interpolate: False
run_current: 0.7
sense_resistor: 0.220
stealthchop_threshold: 0                                            # Set to 999999 to turn stealthchop on, and 0 to use spreadcycle
diag_pin: ^PA3                                                      # YOU NEED TO JUMP THIS DIAG PIN ON YOUR BOARD FOR SENSORLESS HOMING TO WORK 
driver_SGTHRS: 100                                                  # this is set to 255 which is the MAX sensitivity for sensorless homing, you will need to tune this later

#####################################################################
#   Z Stepper Settings
#####################################################################

[stepper_z]
step_pin: PB4
dir_pin: !PB5	                                                    # Remove the ! before PB8 if motor direction is inverted.
enable_pin: !PC2
rotation_distance: 8                                                # For T8x8 lead screw
#rotation_distance: 2                                               # For T8x2 lead screw
microsteps: 32
endstop_pin: ^PC4
position_endstop: 119.6
position_max: 120
position_min: -1.5
homing_speed: 20
second_homing_speed: 3.0
homing_retract_dist: 3.0

[tmc2209 stepper_z]
uart_pin: PB3
#tx_pin: PA2
uart_address: 2
interpolate: False
# For FYSETC 42HSC1404B-200N8
run_current: 0.3
sense_resistor: 0.220
stealthchop_threshold: 0                                             # Set to 999999 to turn stealthchop on, and 0 to use spreadcycle

#####################################################################
#   Extruder
#####################################################################

[extruder]
step_pin: PB2
dir_pin: !PA15	                # Add ! if moving opposite direction
enable_pin: !PD2
full_steps_per_rotation: 200    # Set to 200 for 1.8 degree motor, set to 400 for 0.9 degree stepper motor
rotation_distance: 22.23        # See calibrating rotation_distance on extruders doc
gear_ratio: 50:10               # For Mini Afterburner
microsteps: 32
nozzle_diameter: 0.400
filament_diameter: 1.750
heater_pin: PC7
## Check what thermistor type you have. See https://www.klipper3d.org/Config_Reference.html#common-thermistors for common thermistor types.
## Use "Generic 3950" for NTC 100k 3950 thermistors
sensor_type: Generic 3950
sensor_pin: PC5
control: pid            # Do PID calibration
pid_Kp: 28.182
pid_Ki: 1.978
pid_Kd: 100.397
min_temp: 0
max_temp: 270
min_extrude_temp: 170
max_extrude_only_distance: 150
max_extrude_cross_section: 1.5
pressure_advance: 0.0   # See tuning pressure advance doc
pressure_advance_smooth_time: 0.040

[tmc2209 extruder]
uart_pin: PB3
#tx_pin: PA2
uart_address: 3
interpolate: False
run_current: 0.7
sense_resistor: 0.220
stealthchop_threshold: 0                                            # Set to 0 for spreadcycle, avoid using stealthchop on extruder

#####################################################################
#   Bed Heater
#####################################################################

[heater_bed]
heater_pin: PC8
## Check what thermistor type you have. See https://www.klipper3d.org/Config_Reference.html#common-thermistors for common thermistor types.
## Use "Generic 3950" for Keenovo heaters
sensor_type: Generic 3950
sensor_pin: PB0
smooth_time: 3.0
#max_power: 0.6                                                      # Only needed for 100w pads
min_temp: 0
max_temp: 120
control: pid                                                         # Do PID calibration after initial checks
pid_kp: 68.453
pid_ki: 2.749
pid_kd: 426.122

#####################################################################
# Fan Control
#####################################################################

[heater_fan hotend_fan]
# FAN1 Connector
pin: PA13
max_power: 1.0
kick_start_time: 0.5
heater: extruder
heater_temp: 50.0
#fan_speed: 1.0                                                      # You can't PWM the delta fan unless using blue wire

[fan]
# Print Cooling Fan: FAN0 Connector
pin: PA14
max_power: 1.0
kick_start_time: 0.5                                                 # Depending on your fan, you may need to increase this value if your fan will not start
off_below: 0.13
cycle_time: 0.010

[controller_fan MCU_fan]
pin: PA8
max_power: 1.0
kick_start_time: 0.5
heater: extruder
#fan_speed: 1.0 

#####################################################################
# Homing and Gantry Adjustment Routines
#####################################################################

[idle_timeout]
timeout: 1800
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

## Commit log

2023-03-21 Upload data
    Upload data
    [A_Drive_Frame_Lower_x1.stl, A_Drive_Frame_Upper_x1.stl, A_Idler_Lower_x1.stl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]
2023-03-22 update firmware
    update firmware
    [printer.cfg]
2023-03-23 Upload Wiring
    Upload Wiring
2023-03-28 update wiring
    update wiring
2023-07-07 Add R1 version data
    Add R1 version data
    [A_Drive_Frame_Lower_x1.stl, A_Drive_Frame_Upper_x1.stl, A_Idler_Lower_x1.stl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]
2023-08-22 Update information
    Update information
    [Rear_Skirt_x1.STL]
2023-10-19 Fix powersupply wiring error
2023-10-19 Create BOM.md
    created a separate BOM file
2023-10-19 Improve documentation
    Renamed additional STLs to better describe it and to follow Voron standards
    Updated Readme
    [Bed_Wago_Mount_x1.STL, Drag_Chain_Spacer_x1.STL, Fan_Mount_x1.stl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]
2023-10-21 Fix wiring jpg link
2023-10-26 Modify A、B_Drive_Frame_Upper
    Modify A、B_Drive_Frame_Upper to increase the gap and prevent it from being stunned
    [A_Drive_Frame_Upper_Rev1_x1.STL, A_Drive_Frame_Upper_x1.stl, B_Drive_Frame_Upper_Rev1_x1.STL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]
2023-11-08 Fix sensor_resistor for FYSETC cheetah 3.0
    Correct the sensor resistor settings for cheetah 3.0. The 2.0 and 3.0 both have dual 220Rs, the cheetah 1.2 and the 2209 standalone drivers had the 110Rs.
    @GerogeFu submitted the cheetah 3.0 to Voron's v0 github recently with the correct values. https://github.com/VoronDesign/Voron-0/pull/324/commits/c60e18767d7f378fdfdc9439707bd4af4f4c70fd
    [printer.cfg]
2023-11-21 Adding files for the Catalyst Board in the kit
    [CATALYST_Mount01_x2.STL, CATALYST_Mount02_x1.STL, CATALYST_Mount03_x3.STL]
2023-11-25 Update Readme.md
    Update to mention that the unecessary bed parts were removed and removing the link to the official Voron repo.
2023-11-25 Removing Stock Bed parts
    Removing the stock bed parts so that the files list is easier to understand and more concise.
    [Drag_Chain_Spacer_x1.stl, Front_Bed_Mount_x1.stl, Rear_Bed_Mount_Left_x1.stl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]
2024-01-27 Upload 0.2R1 Pro V1.1 data
    Upload 0.2R1 Pro V1.1 data
    [A_Drive_Frame_Lower_x1.stl, A_Drive_Frame_Upper_Rev1_x1.STL, A_Idler_Lower_x1.stl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]
2024-01-27 Upload V1.1 BOM
    Upload V1.1 BOM
2024-04-30 Upload the STL file
    Upload the STL file for 0.2 pro CNC
    [BMG_Shaft_Mod_Spacer_x1.STL, Bed_Wago_Mount_x1.STL, Display_Knob_x1.stl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]
